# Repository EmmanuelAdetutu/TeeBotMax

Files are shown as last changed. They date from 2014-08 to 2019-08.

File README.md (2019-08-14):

TeeBotMax
=========

The design is highly inspired by the fantastic Foldarap and Prusa I3 3D printers. I needed a 3D printer I can fold and carry around easily.
The idea was to develop a high qiality 3D printer which is simple to build and at the same time, easy to move around and travel with, built with simple materials and equally strong and precise.

Blog, Photo, Info:  http://tutuemma.wordpress.com/3d-stuffs/teebotmax/

Build Video Part 1: https://www.youtube.com/watch?v=Mo2O-83_jfQ

<b>TeeBot suitcase 3D printer.</b><br>
The second iteration of the design resulted in a version that fits and works in a suitcase!! the project was successfully funded via kickstater (https://www.kickstarter.com/projects/99905999/teebot-the-suitcase-3d-printer)

Version2  
=========

Many thanks to builders and contributors who have been giving the feedbacks, there is an update version of the TeebotMax featured with Auto-Bed leveling, strong modified plastic parts and other cool fixes.

<b>***folow me on instagram...  </b>[#teebot3d](https://www.instagram.com/teebot3d/)

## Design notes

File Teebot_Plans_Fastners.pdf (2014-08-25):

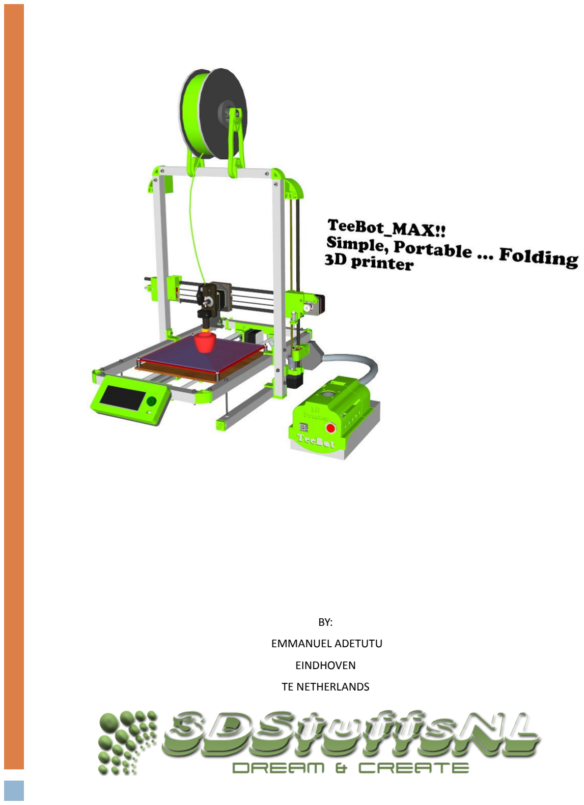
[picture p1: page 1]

BY:

EMMANUEL ADETUTU

EINDHOVEN

TE NETHERLANDS

7/18/2014 | TeeBotMax | 1

### TABLE OF CONTENTS

ABOUT The MANUAL | 2
The design & Specification | 3
Specification | 1
Fastners | 2

ABOUT THE MANUAL.

This manual provides you with a visual step by step guide on how to build or assemble TeeBotMax 3D printer. For more build photos please visit my blog, you will have to source the material/parts needed for your build according to the design.

Many will like to start with a complete/ partial kit, you can grab one directly here (www.3dstuffs.nl/webstore/)

Please report any error detected in this documentation.

I do all of my drawing in Sketchup and a big fan of the software.

Feel free to get in touch, if you have related questions, collaboration enquiry, or just simply talk 3D printing

For photos and videos of the 3D printer in action, visit my web blog

### How to contact

Twitter : @teebotmax

Google plus TeebotMax (https://plus.google.com/u/0/b/106611509110430377536/106611509110430377536/posts)

Web Blog tutuemmaWordpress (https://tutuemma.wordpress.com/)

You can grab a 3D printer kit or needed parts here (www.3dstuffs.nl/webstore/)

I hope this guide helps or inspire you in building or assembling your own 3D printer!! If you do please send me a photo of your build.

THE DESIGN & SPECIFICATION.

The Idea was to design and build a 3D printer which is simple to assemble, easy to move around and travel with, using simple easy to get materials and equally strong and precise.
Many open source designed 3D printer have inspired me in the design of TeeBotMax. Many thanks for sharing: to all the open source developers worldwide over.
**Special thanks to - Josef Prusa (Prusa I3), Emmanuel Gilloz (FoldaRap), Richard Horne (Richrap), Reifsnyderb (J head Hotend) just to mention a few.

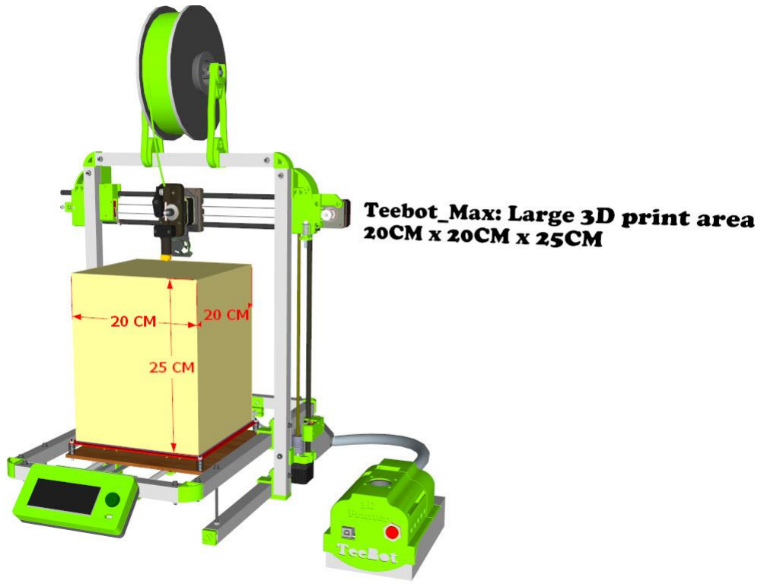
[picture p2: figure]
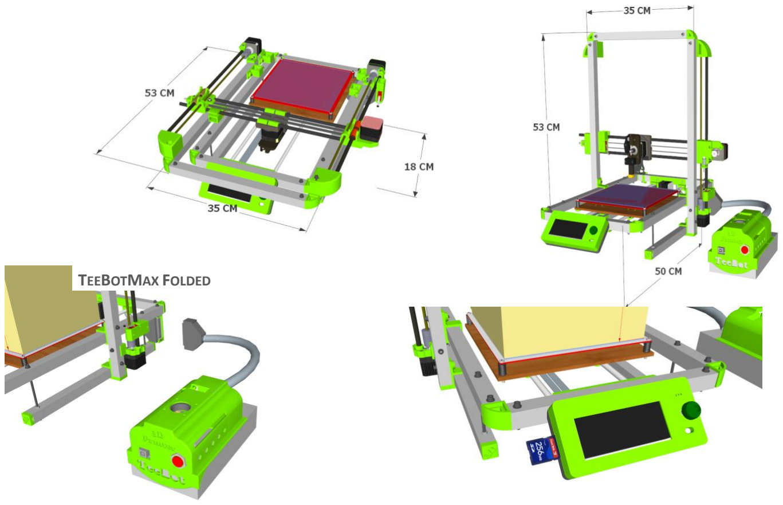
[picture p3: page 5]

TEEBOTMAX FOLDED

SPECIFICATION.

- Build Cost: 350 ~500 Euro (Depending on source of materials/parts)
- Build time: Approximately 1 full day.
- Filament type: Compatible with 3mm/1.75mm, ABS/PLA/Flexible_filament
- Print Speed: 120mm/s
- Nozzle: J head type 0.4mm
- Tested Layer height/resolution: 0.1mm
- Power supply: 12v 20a
- Weight: ~7kg

FASTNERS.

### Footer

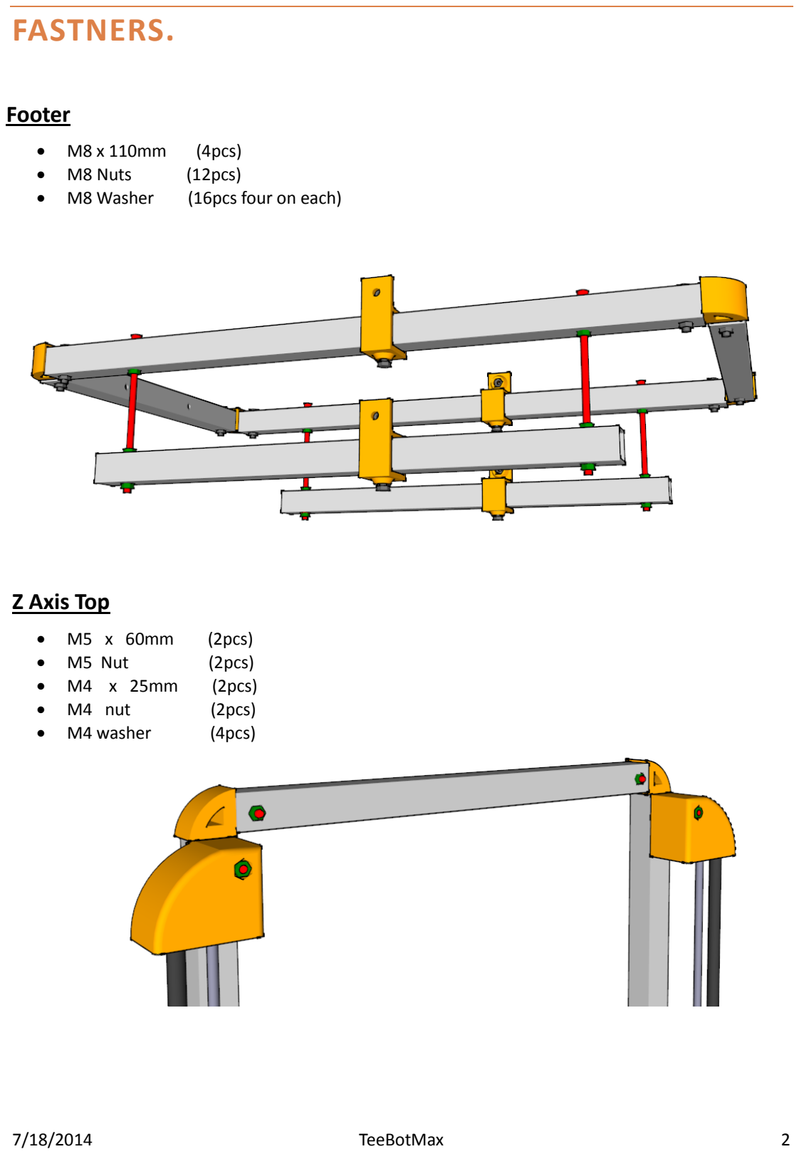
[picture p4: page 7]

- | M8 x 110mm | (4pcs)
- | M8 Nuts | (12pcs)
- | M8 Washer | (16pcs four on each)

### Z Axis Top

- | M5 x 60mm | (2pcs)
- | M5 Nut | (2pcs)
- | M4 x 25mm | (2pcs)
- | M4 nut | (2pcs)
- | M4 washer | (4pcs)

### Z Axis Bottom

- M4 x 30mm (4pcs)
- | M4 washer | (4pcs)
- | M4 Nut | (4pcs)

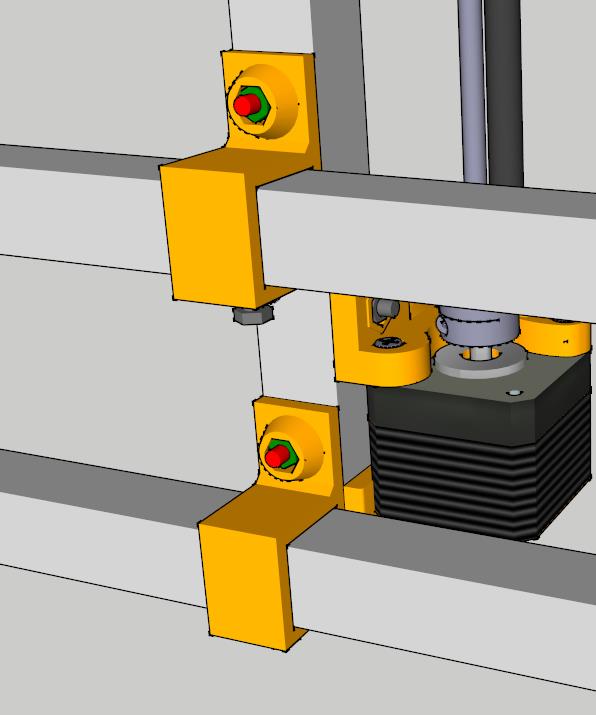
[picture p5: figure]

### Z Axis lock

- M4 x 10mm (4pcs)
- | M4 nuts | (4pcs)

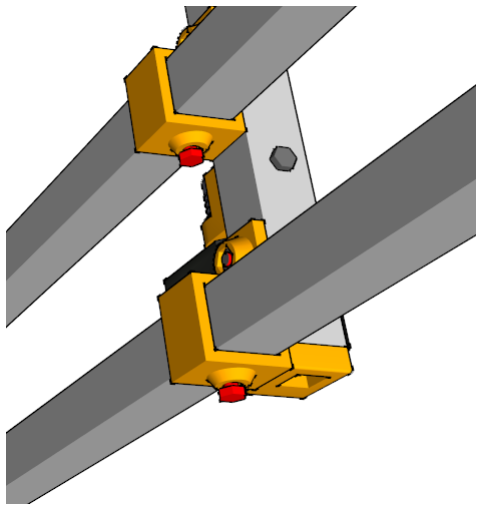
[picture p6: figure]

### Z Motor Holder

- | M4 | x 30mm (2pcs)
- | M4 Nuts | (2pcs)
- | M4 Washer | (2pcs)
- M3 x 10mm (6pcs)

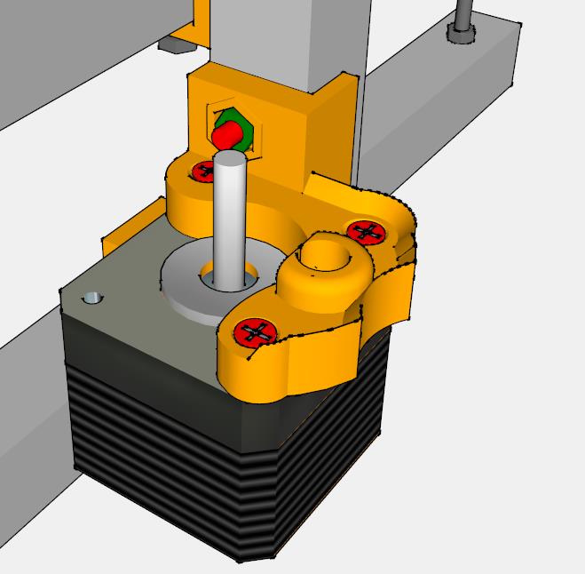
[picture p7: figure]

### Four corner

- | M4 x 25mm | (8pcs)
- | M4 Nuts | (8pcs)
- | M4 washers | (16pcs)

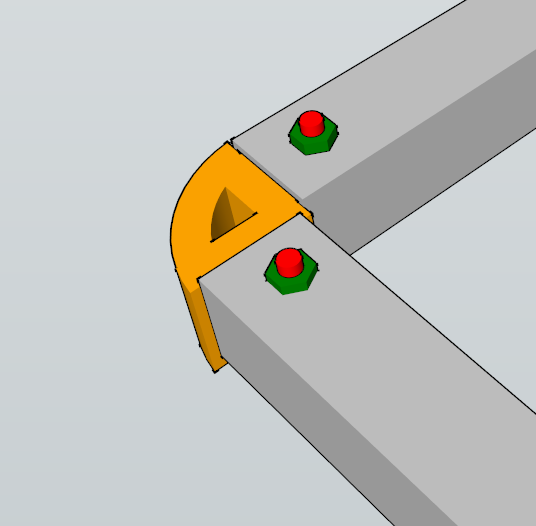
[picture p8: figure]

### X Axis

- | M3 x 10mm | (3pcs)
- Flat head M4 x 25mm (2pcs)
- | M4 Nut | (2pcs)
- | M3 x 20mm | (1pcs)
- | M3 nut | (2pcs)

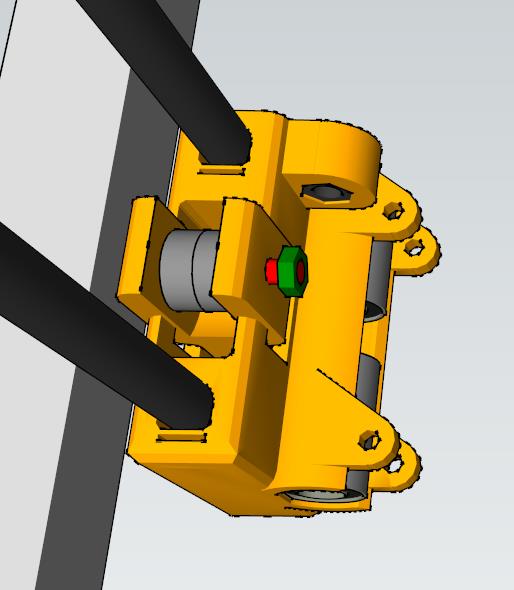
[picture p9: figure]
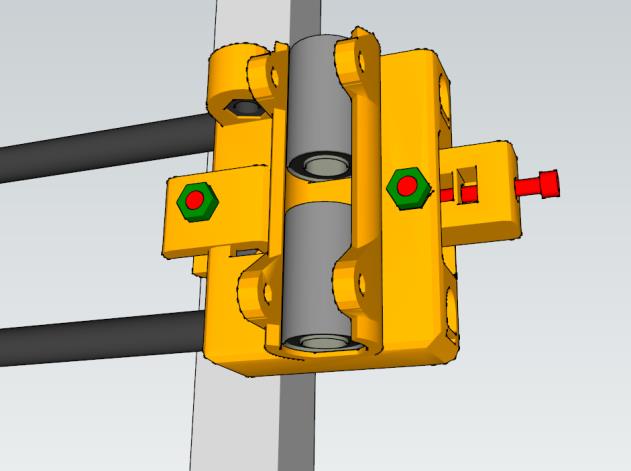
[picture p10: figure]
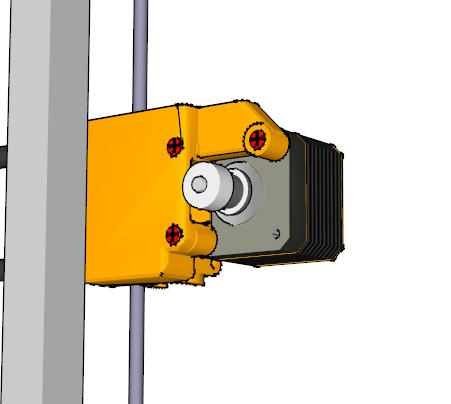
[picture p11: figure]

### Y axis

- M4 x 30mm (1pcs)
- | M4 Nuts | (1pcs)
- | M3 x 30mm | (4pcs)
- | M3 nuts | (4pcs)
- | M3 washer | (8pcs)
- | M3 x 10mm | (3pcs)

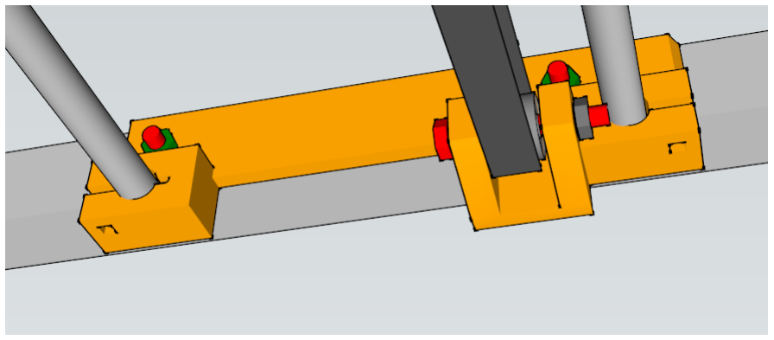
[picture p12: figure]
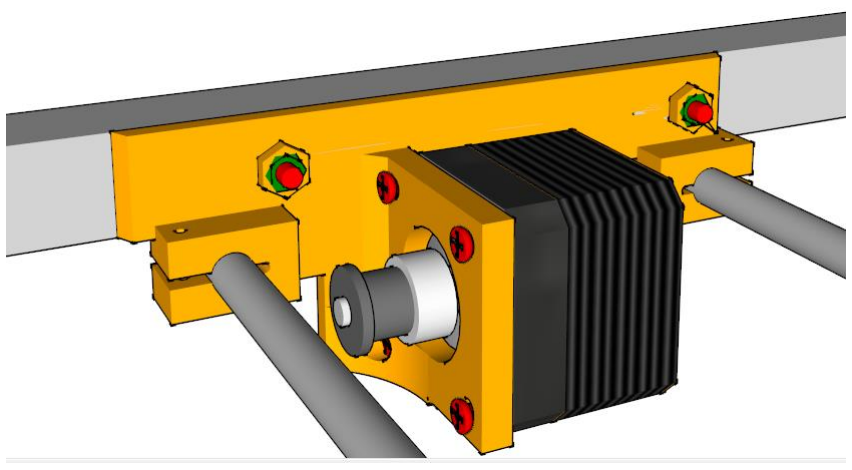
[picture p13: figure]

### Heat Bed

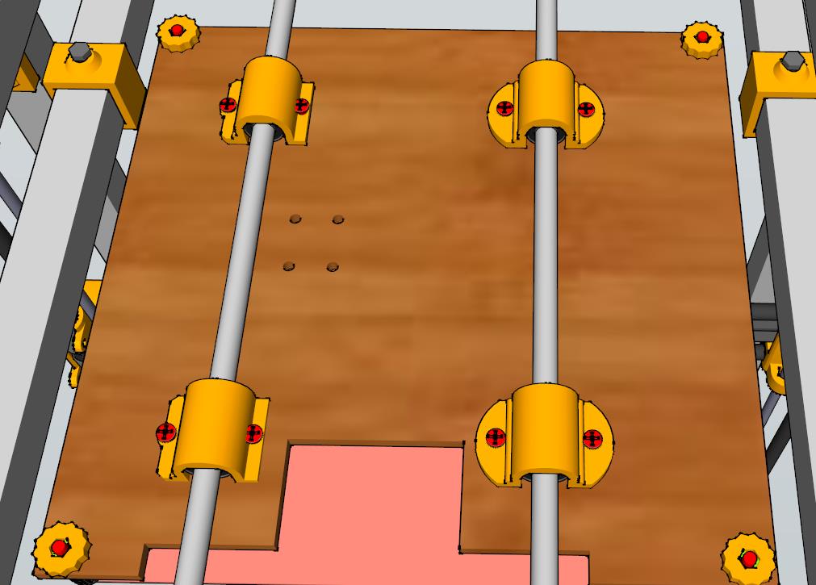
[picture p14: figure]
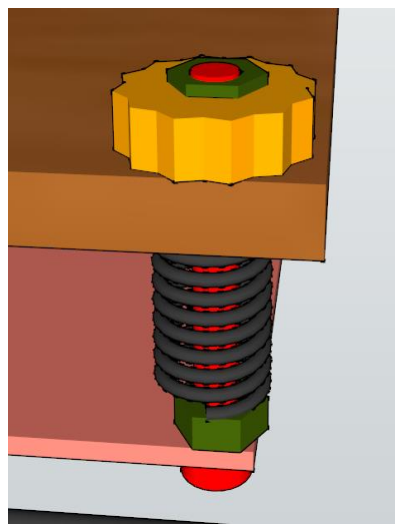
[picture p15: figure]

- M3 x 30mm (4pcs)
- | M3 nuts | (8pcs)
- M3 x 16mm (8pcs)
- M3 washer (8pcs)
- | M3 nuts | (8pcs)

### X Axis carriage

- | M3 x 20mm fan | (2pcs)
- | M3 washer | (4pcs)
- | M3 nut | (2pcs)
- | M4 x 25mm | (4pcs) mount
- | M4 nuts | (4pcs)
- | M 5 nuts | (2pcs) X_axis lift

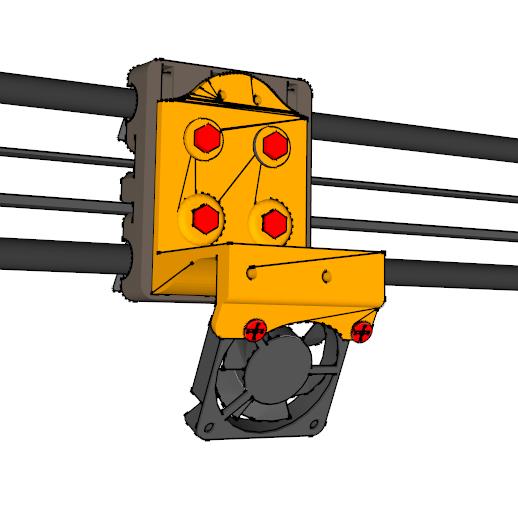
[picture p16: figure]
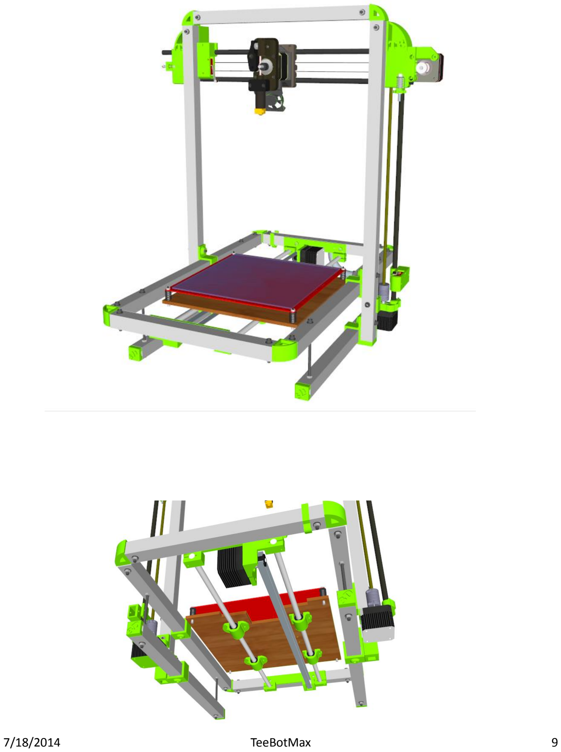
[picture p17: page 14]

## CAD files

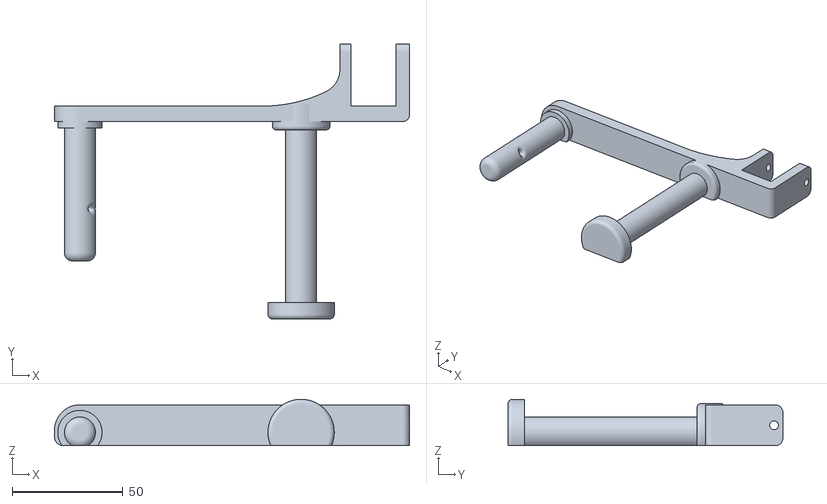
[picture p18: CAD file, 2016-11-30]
STL_Files/SPOOL_FEEDER.stl
160.5 x 124.2 x 21.0

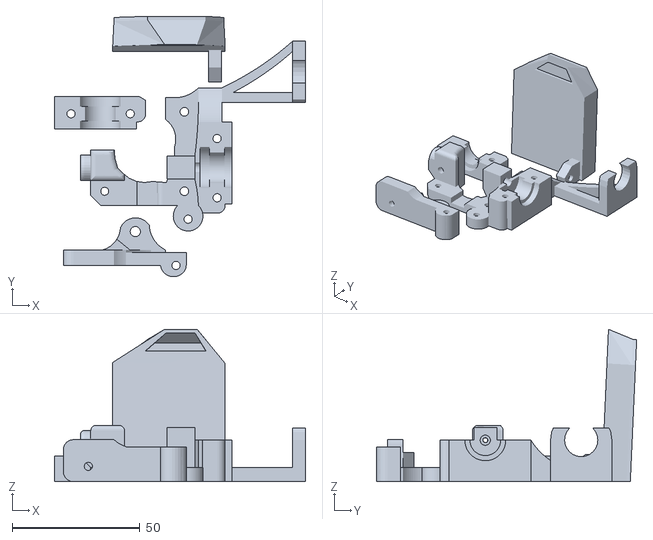
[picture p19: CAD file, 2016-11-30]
STL_Files/Extruder_E3d_Lite.stl
98.2 x 101.8 x 59.6

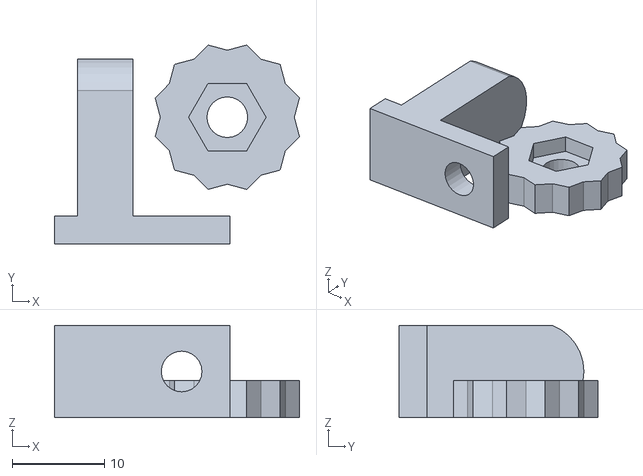
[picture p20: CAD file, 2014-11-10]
STL_Files/Smart_Zlevel.stl
26.5 x 21.5 x 10.0

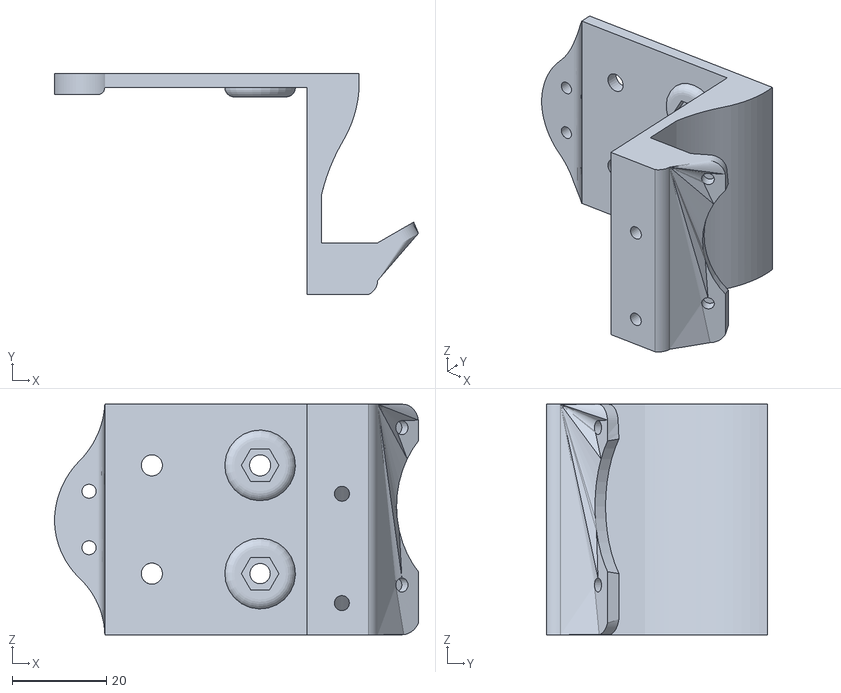
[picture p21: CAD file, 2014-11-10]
STL_Files/X_Extruder_Mount_2.stl
77.4 x 47.0 x 49.0

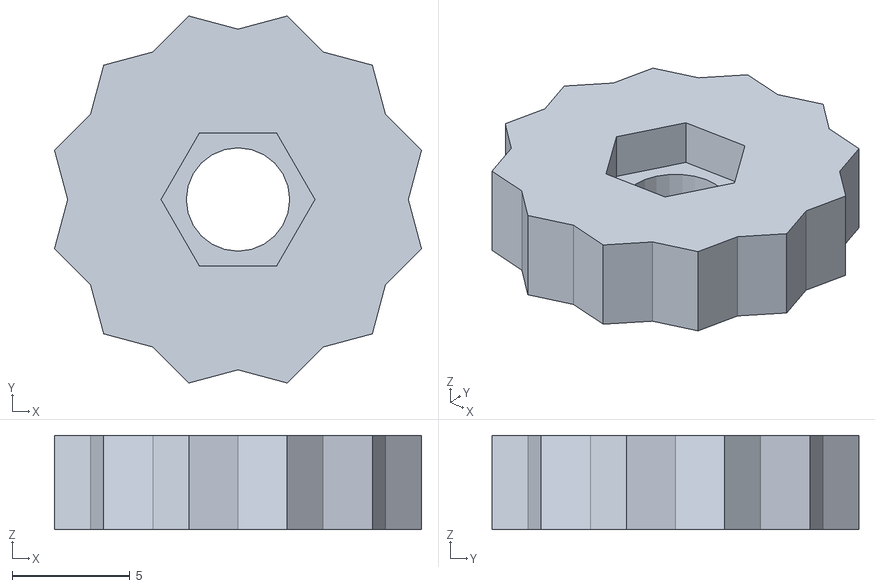
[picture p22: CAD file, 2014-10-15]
STL_Files/Bed_Knobs.stl
15.6 x 15.6 x 4.00

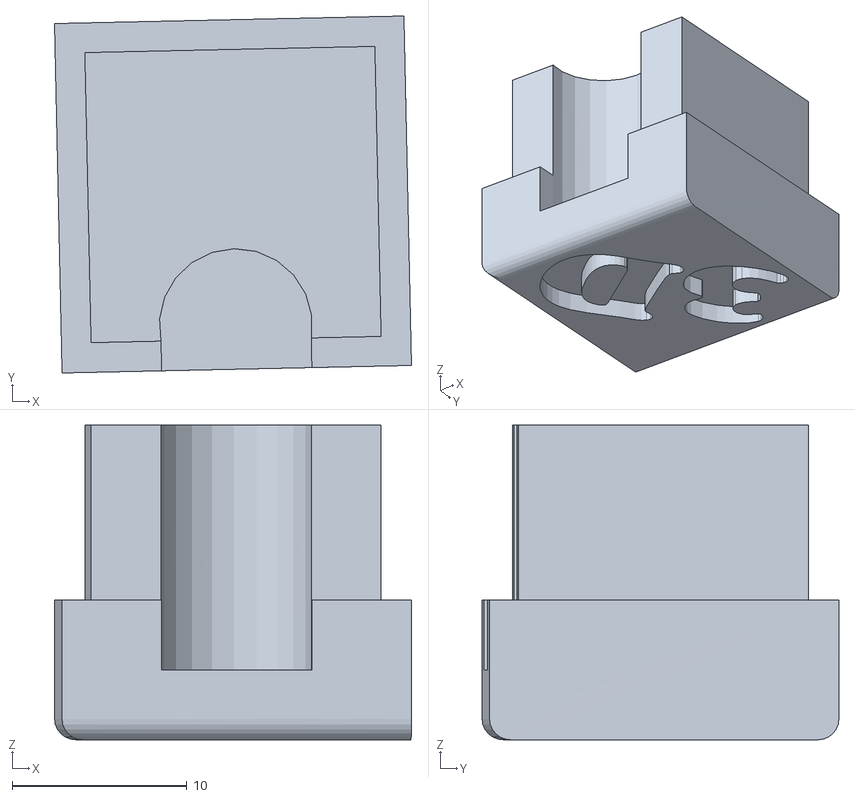
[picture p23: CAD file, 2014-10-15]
STL_Files/Foot_Cap.stl
20.4 x 20.4 x 18.0

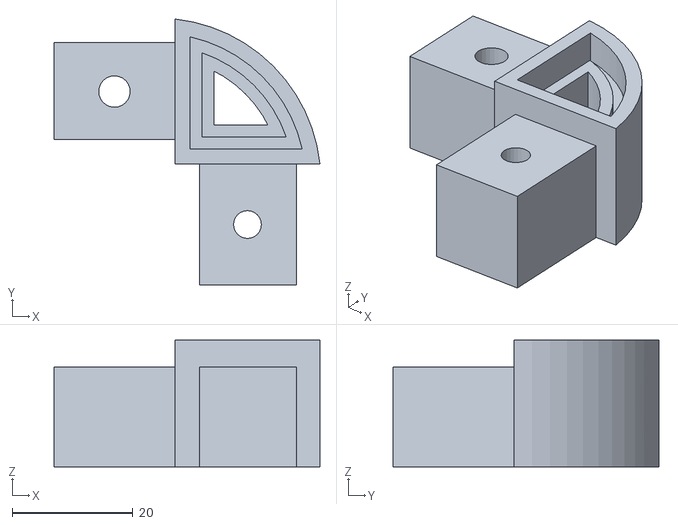
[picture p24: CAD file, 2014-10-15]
STL_Files/Corners.stl
44.0 x 44.0 x 21.0

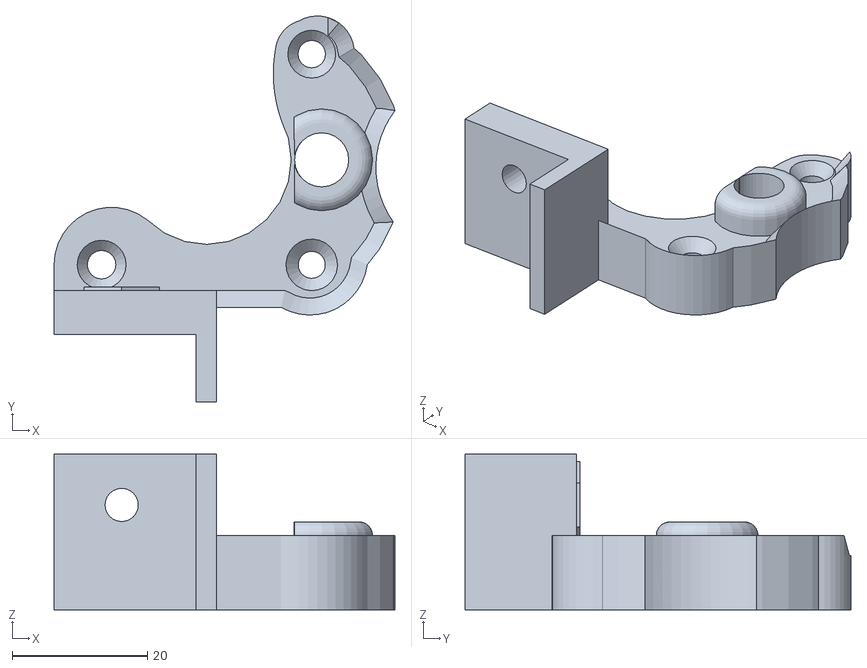
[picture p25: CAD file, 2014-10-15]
STL_Files/Z_End_Motor_R.stl
50.4 x 57.1 x 23.0

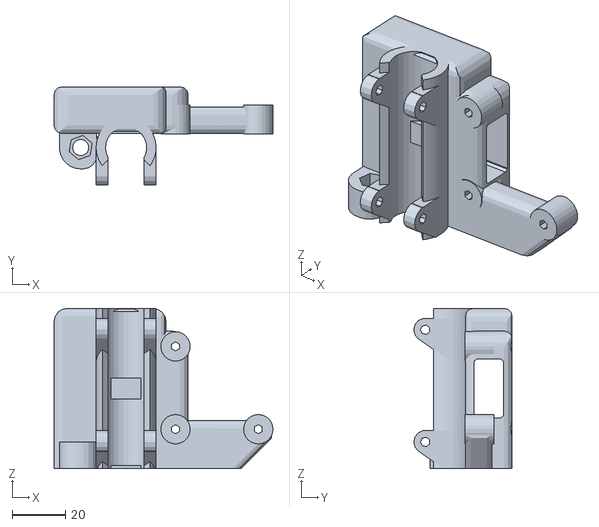
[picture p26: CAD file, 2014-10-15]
STL_Files/X_Ends_R.stl
82.0 x 36.9 x 60.0

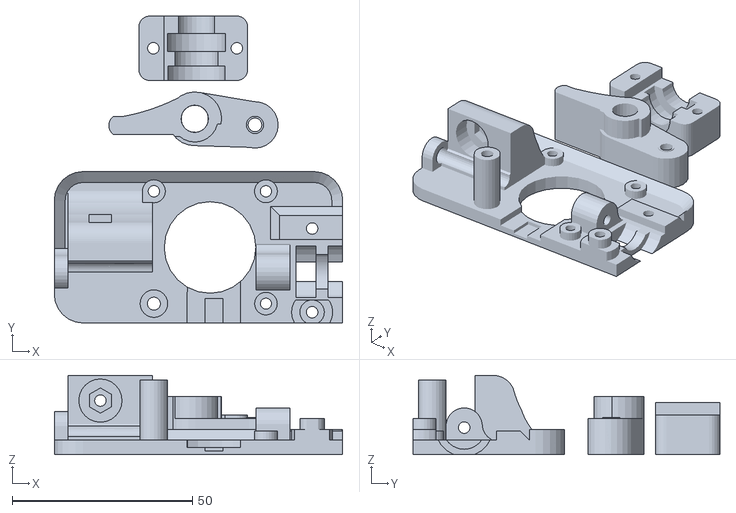
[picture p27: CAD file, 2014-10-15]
STL_Files/Direct_Drive_Extruder.stl
80.0 x 85.1 x 22.0

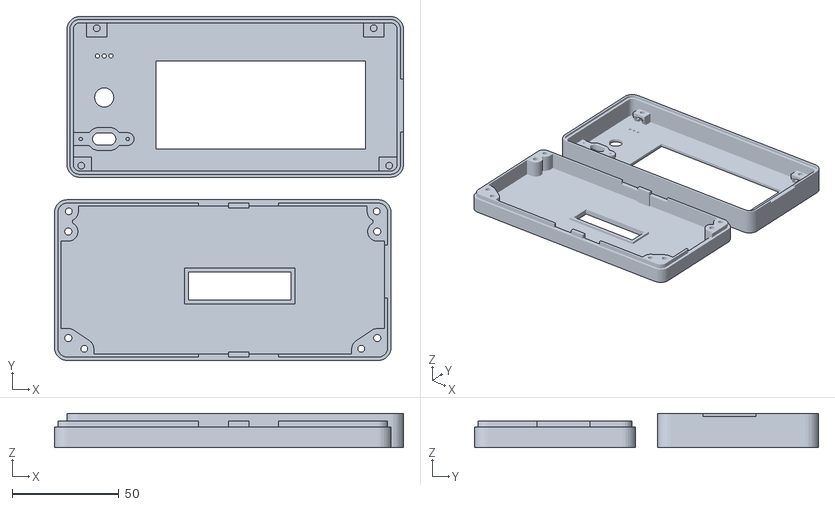
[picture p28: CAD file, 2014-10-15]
STL_Files/SD_Ramps_Case.stl
163.8 x 161.5 x 16.0

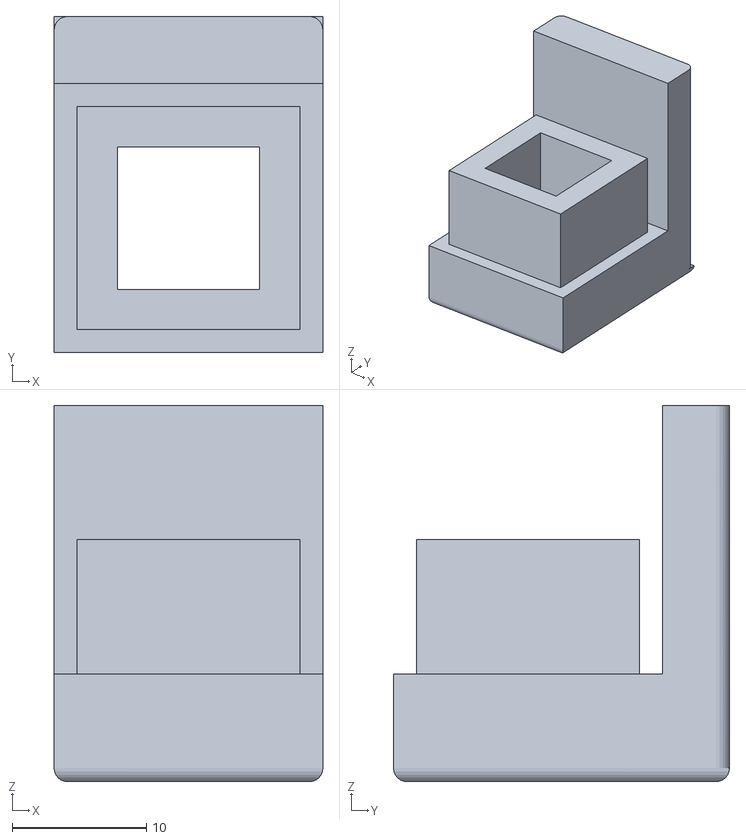
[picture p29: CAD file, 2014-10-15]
STL_Files/Z_Foot_Cap.stl
20.0 x 25.0 x 28.0

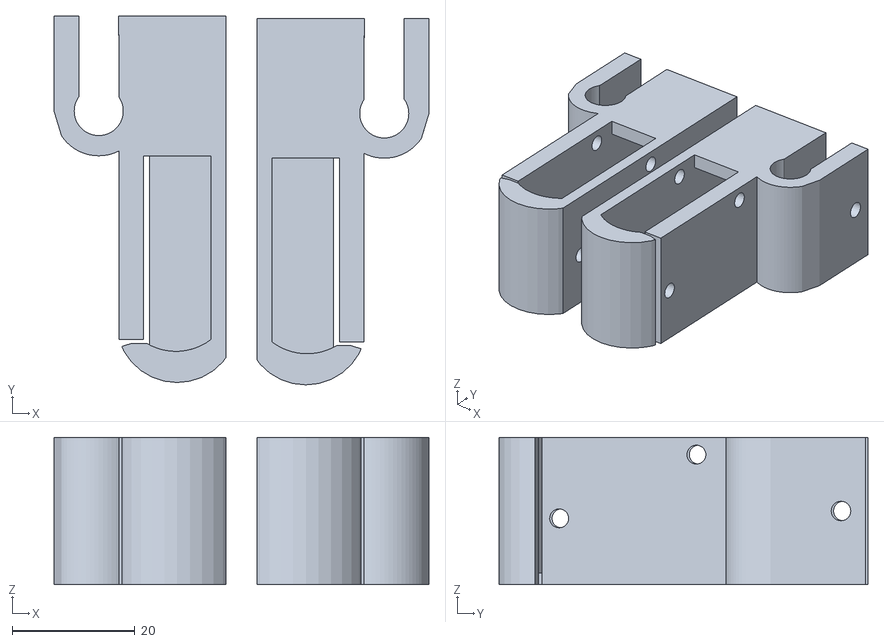
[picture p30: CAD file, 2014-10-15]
STL_Files/Limit Holder.stl
61.2 x 60.2 x 24.0

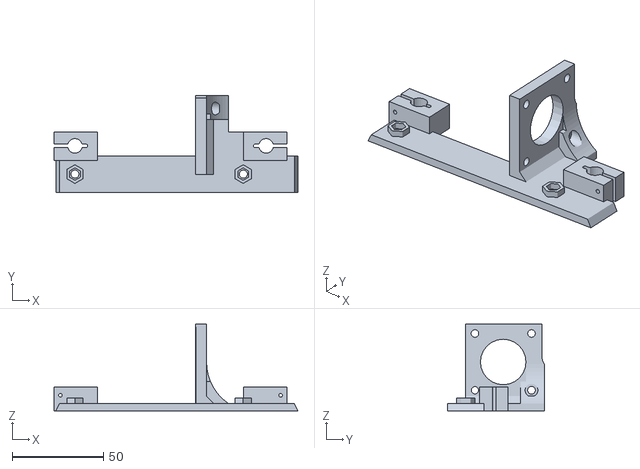
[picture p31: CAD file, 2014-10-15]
STL_Files/Y_End_Motor.stl
134.0 x 53.1 x 47.5

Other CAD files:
STL_Files/Z_End_Motor_L.stl
STL_Files/X_Motor_Iddler.stl
STL_Files/Connectors.stl
STL_Files/Optional Spool holder.stl
STL_Files/Bearing_Holder.stl
STL_Files/Belt_Bearing_Holder.stl
STL_Files/Extruder Extension.stl
STL_Files/Optional_Dsub_Holder.stl
STL_Files/Ramps_casing.stl
STL_Files/X_Ends_L.stl
STL_Files/X_Extruder_Mount.stl
STL_Files/X_carriage.stl
STL_Files/Y_Iddler.stl
STL_Files/Z_Rod_Holder_L.stl
STL_Files/Z_Rod_Holder_R.stl

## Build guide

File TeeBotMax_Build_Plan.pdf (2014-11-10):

BY:

EMMANUEL ADETUTU

EINDHOVEN

TE NETHERLANDS

7/18/2014 | TeeBotMax | 1

### TABLE OF CONTENTS

ABOUT The MANUAL | 2
The design & Specification | 3
Specification | 2
List of Materials Needed | 3
Fastners | 4
Printed parts | 11
Smooth & Threaded ROds | 13
Aluminium frame | 13
print bed support | 0
print bed support | 1
The Build… Part 1 (Main frame) | 4
The Build… Part 2 (Print platform) | 10
The Build… Part 3 (Assembling the X Axis) | 15
The Build… Part 4 (Assembling the Z Axis) | 20
The Build Part 5 (Extruder carriage & belt) | 27
The Build Part 6 (ELECTRONICS & Limit switch) | 32
Limit Switch | 33

ABOUT THE MANUAL.

This manual provides you with a visual step by step guide on how to build or assemble TeeBotMax 3D printer. For more build photos please visit my blog, you will have to source the material/parts needed for your build according to the design.

Many will like to start with a complete/ partial kit, you can grab one directly here (www.3dstuffs.nl/webstore/)

Please report any error detected in this documentation.

I do all of my drawing in Sketchup and a big fan of the software.

Feel free to get in touch, if you have related questions, collaboration enquiry, or just simply talk 3D printing

For photos and videos of the 3D printer in action, visit my web blog

### How to contact

Twitter : @teebotmax

Google plus TeebotMax (https://plus.google.com/u/0/b/106611509110430377536/106611509110430377536/posts)

Web Blog tutuemmaWordpress (https://tutuemma.wordpress.com/)

You can grab a 3D printer kit or needed parts here (www.3dstuffs.nl/webstore/)

I hope this guide helps or inspire you in building or assembling your own 3D printer!! If you do please send me a photo of your build.

THE DESIGN & SPECIFICATION.

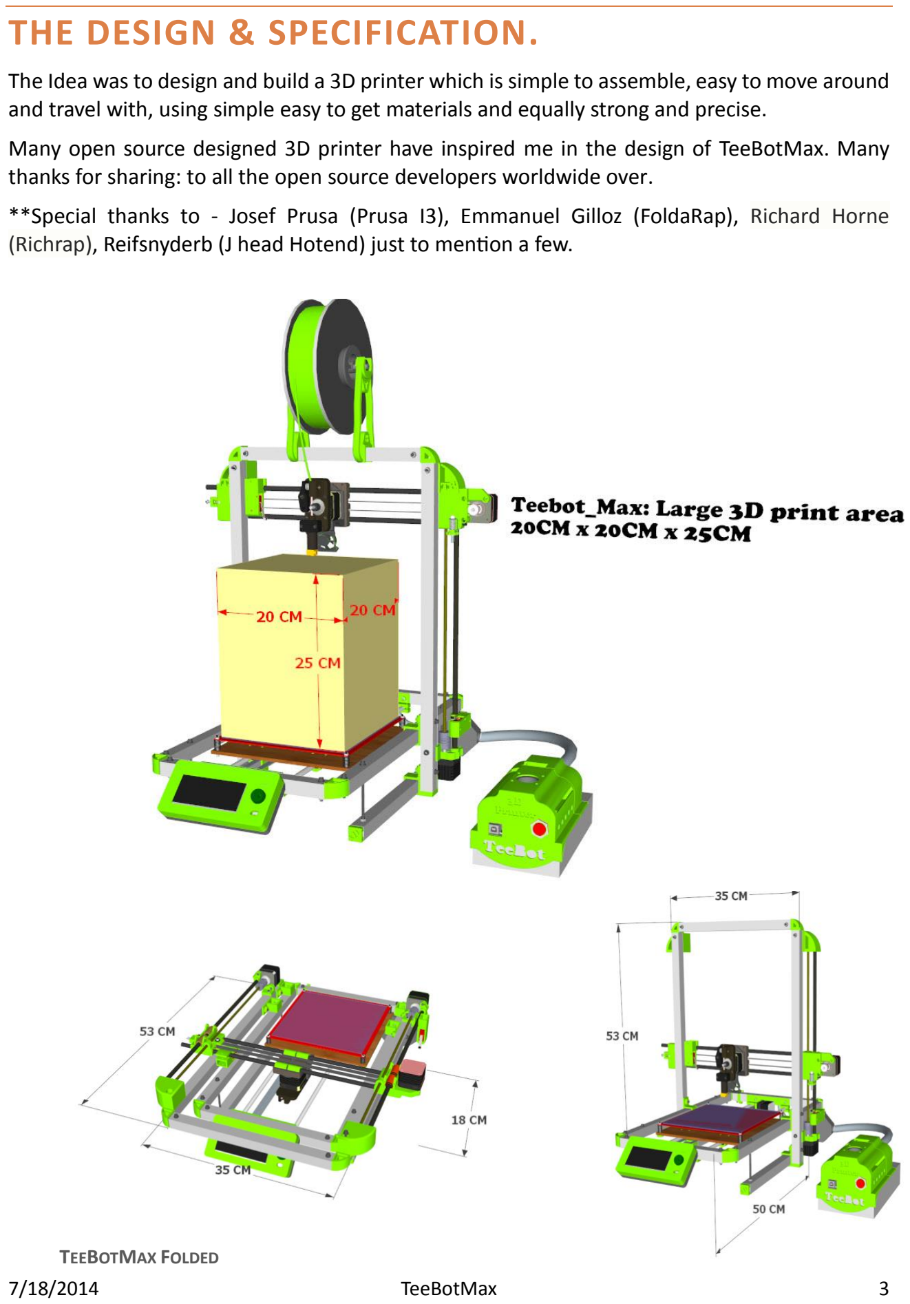
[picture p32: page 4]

The Idea was to design and build a 3D printer which is simple to assemble, easy to move around and travel with, using simple easy to get materials and equally strong and precise.
Many open source designed 3D printer have inspired me in the design of TeeBotMax. Many thanks for sharing: to all the open source developers worldwide over.
**Special thanks to - Josef Prusa (Prusa I3), Emmanuel Gilloz (FoldaRap), Richard Horne (Richrap), Reifsnyderb (J head Hotend) just to mention a few.

TEEBOTMAX FOLDED

SPECIFICATION.

- Build Cost: 350 ~500 Euro (Depending on source of materials/parts)
- Build time: Approximately 1 full day.
- Filament type: Compatible with 3mm/1.75mm, ABS/PLA/Flexible_filament
- Print Speed: 120mm/s
- Nozzle: J head type 0.4mm
- Tested Layer height/resolution: 0.1mm
- Power supply: 12v 20a
- Weight: ~7kg

LIST OF MATERIALS NEEDED.

SN | Material | Description | Quantity | Note/Source
1 | All Printed plastic parts | You can print or Buy | 1 set
2 | Extruder kit (TeeStruder) | Direct drive extruder. | 1 set
3 | Printer Frame aluminum | 20mm square | 3.4 meters
4 | 8mm Smooth rods | Used in all Axis | 3 meters
5 | Linear bearing Lm8uu | 8 mm | 11 Pcs
6 | Springs Heatbed exturder. | O.D: 10mm | 6 Pcs
7 | 624 Bearing | Used as idlers | 5 Pcs
8 | Threaded rods | 5mm diameter | 1 meter
9 | Flexible shaft coupler | 5mm X 5mm | 5 Pcs
10 | Heated Bed | 12v Heated bed | 1 Pcs
| Print Glass/ mirror | 20cm x 20cm | 1pcs
11 | Complete Electronics Board | Ramps 1.4 | 1 Set
12 | Cooling Fan | 4Cm X 4Cm X 1Cm | 2 Pcs
13 | Power Supply | 12v with min of 15A | 1 Set
14 | Hotend | J head type | 1 Set
15 | 100k Thermistor. | Heated_bed & extruder. | 2 Pcs
16 | Limit switch | One for each axis | 3
17 | Ramps LCD controller | Print without a PC/Laptop | 1
18 | GT2 Timing Belt | Drive’s the X & Y axis | 2 meters
19 | Pulley | Gt2 Pulley | 2
20 | Stepper Motors | Nema 17 | 5 Pcs
| Binder Clips | standard | 4 Pcs

For a complete detail list of fasters please see the section below

FASTNERS.

### Footer

- | M8 x 110mm | (4pcs)
- | M8 Nuts | (12pcs)
- | M8 Washer | (16pcs four on each)

### Z Axis Top

- | M5 x 60mm | (2pcs)
- | M5 Nut | (2pcs)
- | M4 x 25mm | (2pcs)
- | M4 nut | (2pcs)
- | M4 washer | (4pcs)

### Z Axis Bottom

- M4 x 30mm (4pcs)
- | M4 washer | (4pcs)
- | M4 Nut | (4pcs)

### Z Axis lock

- M4 x 10mm (4pcs)
- | M4 nuts | (4pcs)

### Z Motor Holder

- | M4 | x 30mm (2pcs)
- | M4 Nuts | (2pcs)
- | M4 Washer | (2pcs)
- M3 x 10mm (6pcs)

### Four corner

- | M4 x 25mm | (8pcs)
- | M4 Nuts | (8pcs)
- | M4 washers | (16pcs)

### X Axis

- | M3 x 10mm | (3pcs)
- Flat head M4 x 25mm (2pcs)
- | M4 Nut | (2pcs)
- | M3 x 20mm | (1pcs)
- | M3 nut | (2pcs)

### Y axis

- M4 x 30mm (1pcs)
- | M4 Nuts | (1pcs)
- | M3 x 30mm | (4pcs)
- | M3 nuts | (4pcs)
- | M3 washer | (8pcs)
- | M3 x 10mm | (3pcs)

### Heat Bed

- M3 x 30mm (4pcs)
- | M3 nuts | (8pcs)
- M3 x 16mm (8pcs)
- M3 washer (8pcs)
- | M3 nuts | (8pcs)

### X Axis carriage

- | M3 x 20mm fan | (2pcs)
- | M3 washer | (4pcs)
- | M3 nut | (2pcs)
- | M4 x 25mm | (4pcs) mount
- | M4 nuts | (4pcs)
- | M 5 nuts | (2pcs) X_axis lift

PRINTED PARTS.

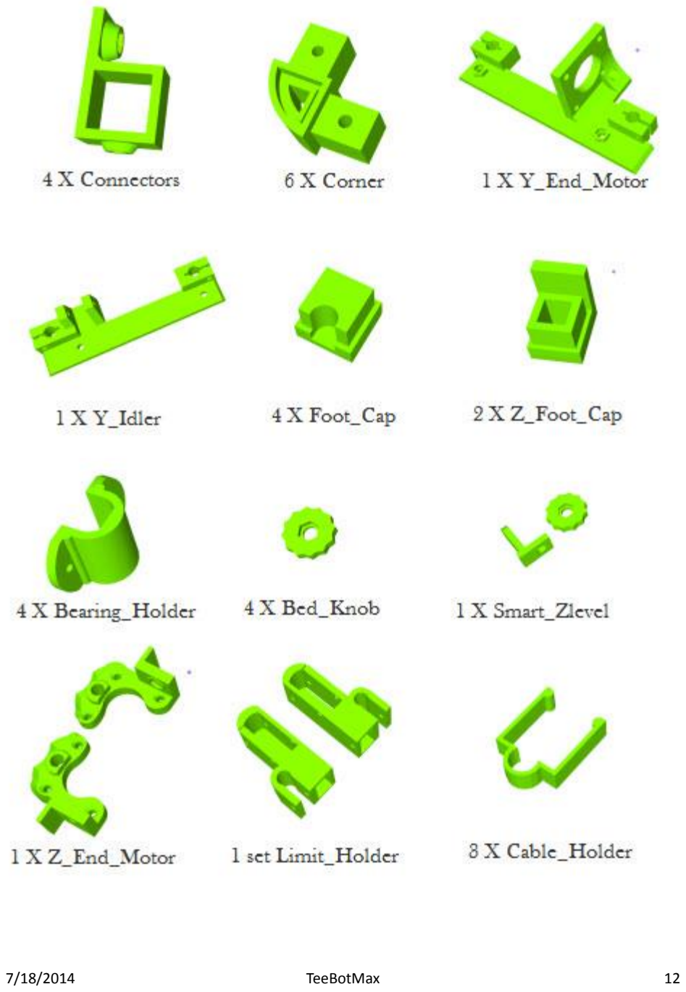
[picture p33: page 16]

SMOOTH & THREADED RODS.

- 2x Smooth rod Ø8 x 460mm
- 4x Smooth rod Ø8 x 420mm
- 2x Threaded rod M5 x 400mm

ALUMINIUM FRAME.

The frame pipes are cut out of 2cm square tubing. 9 Pcs

A. 25cm x 2Pcs | {short main frame}
B. 46cm x 2Pcs | {Long main frame}
C. 50cm x 2Pcs | {Long folding arms}
D. 30cm x 1Pcs | {Folding arms connect}
E. 36cm x 2Pcs | {Foot pipes}

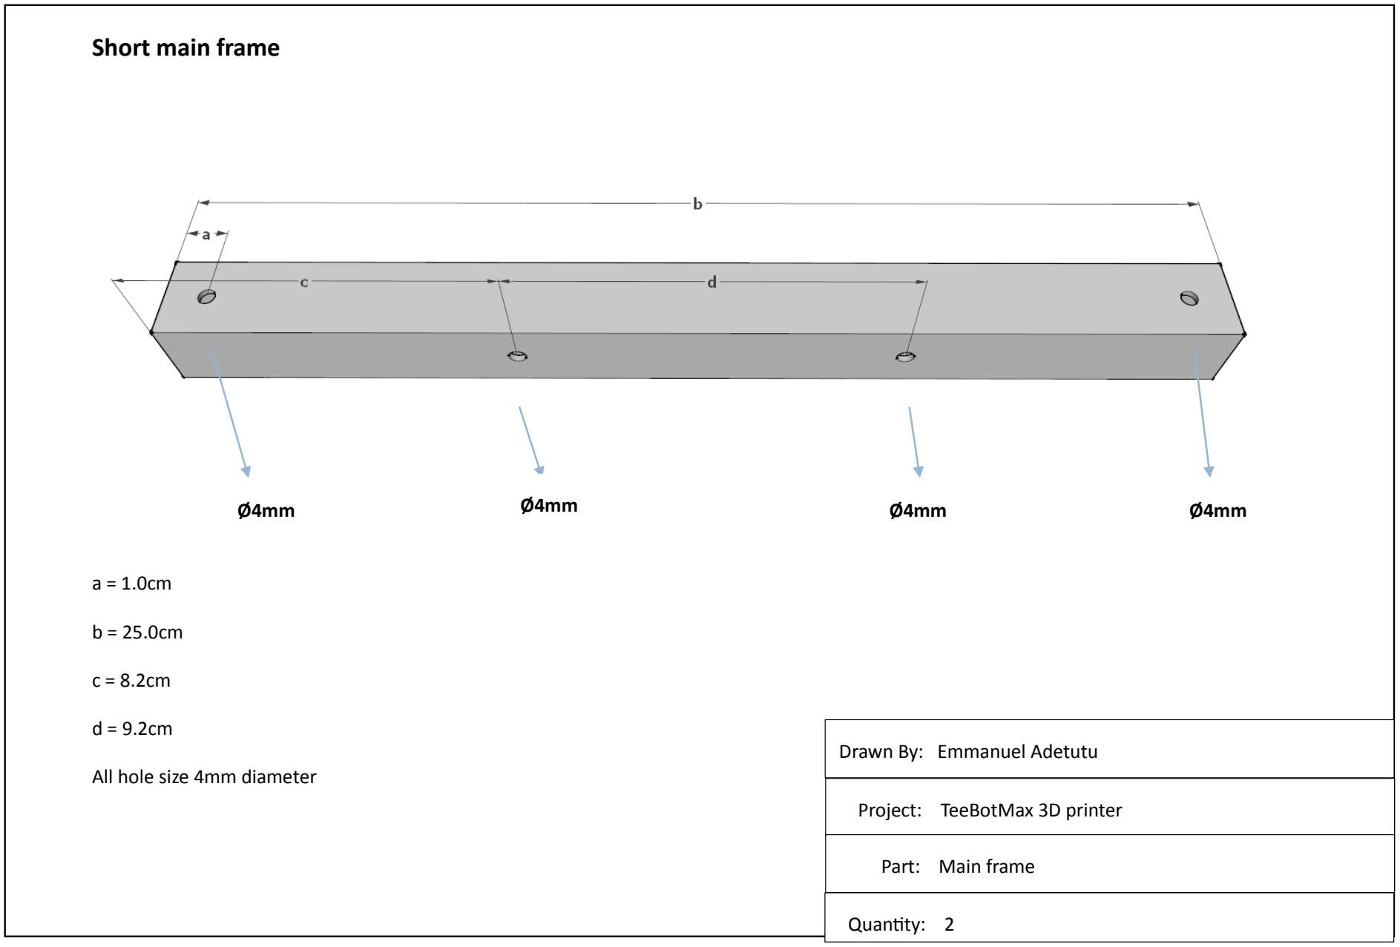
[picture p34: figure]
Short main frame; All hole size 4mm diameter; Drawn By: Emmanuel Adetutu; Project: TeeBotMax 3D printer; Part: Main frame; Quantity: 2

### Long main frame

a = 1.0 cm

b = 6.0 cm

c = 6.0cm

d = 46.0cm

Project: TeeBotMax 3D printer

Part: Main frame

Quantity: 2

Ø8mm | Ø4mm
Ø4mm | Ø8mm

### Long folding arms

a = 1.0cm

b = 6.2cm

c = 50.0cm

d = 3.0cm

e = 11.0cm

Quantity: 2

Part: Z axis frame

Project: TeeBotMax 3D printer

Drawn By: Emmanuel Adetutu

Ø4mm

Ø4mm

Ø4mm

### Short folding arms

a = 1.0cm

b = 30.0cm

c = 1.0cm

Quantity: 1

Part: Z axis frame top

Project: TeeBotMax 3D printer

Drawn By: Emmanuel Adetutu

Ø4mm
Ø4mm

a = 2.0cm

b = 2.0cm

c = 36.0cm

The hole size 8mm diameter

Quantity: 2

Part: footer

Project: TeeBotMax 3D printer

Drawn By: Emmanuel Adetutu

Ø8mm | Ø8mm

PRINT BED SUPPORT

PRINT BED SUPPORT

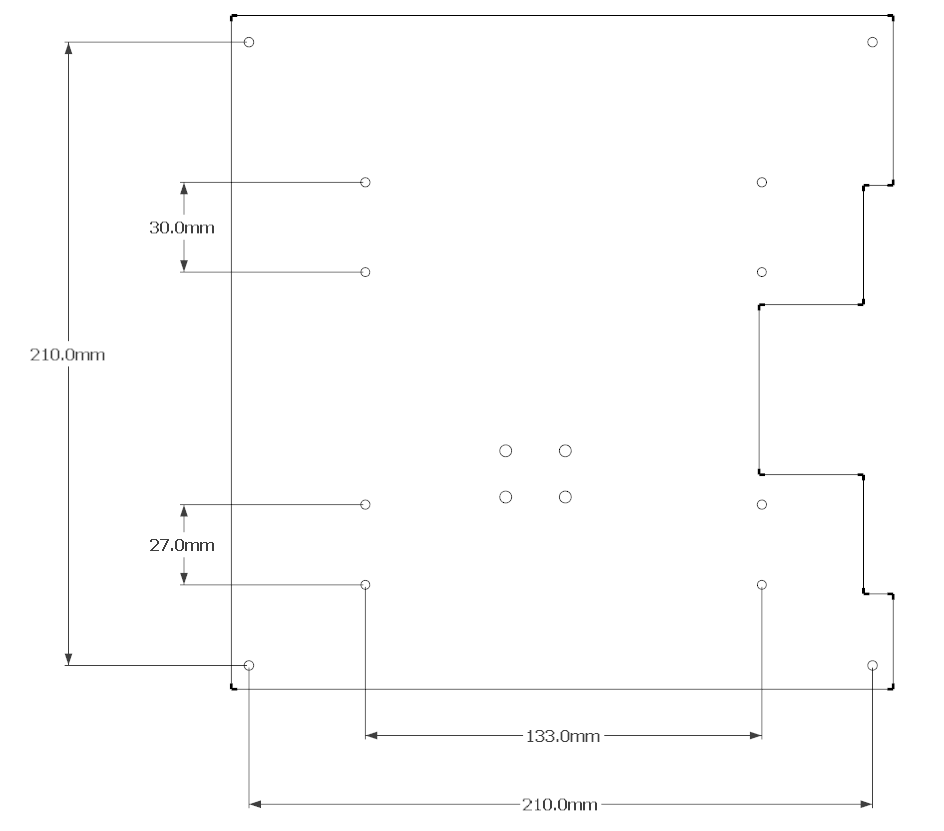
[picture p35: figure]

7/18/2014 | TeeBotMax

2

A = 215mm B = 178mm C = 112mm D = 92mm E = 45mm F = 6mm

A = 35mm

B = 62mm

C = 86mm

D = 56mm

E = 146 mm

F = 162mm

# THE BUILD… PART 1 (MAIN FRAME)

1. Insert 2pcs of the 4m nuts in one of the connectors as shown below, repeat for all 4 connector.
2. Insert 2 of the connectors into the 46cm and 36cm pipe.

## 4 X

3. Thread the M8 bolt into the pipes using 3 nuts and 4 washers. Ensure that the distance between the pipes is 6cm.

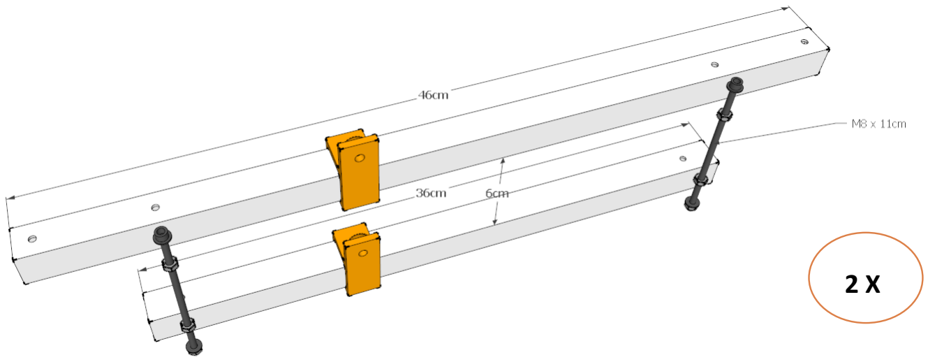
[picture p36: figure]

4. Using M4 x 10mm bolts lock the plastics in place 25cm from the tip of the longer pipe and 20cm from the smaller one as shown below.

Emmanuel Adetutu is a data analyst who works everyday with GIS data in the Netherlands. Likes creating, developing and exploring new tools and application.

My interest in CNC/3D printing started in 2011, when I built my first CNC machine for some wood working projects I have around the house. I started building 3D printers after reading blogs and post by REPRAP developers on the REPRAP.org wiki.

5. Assemble the Y Axis idler as shown below, using the 624 bearing, one M4 bolt and 2 M3 bolts.

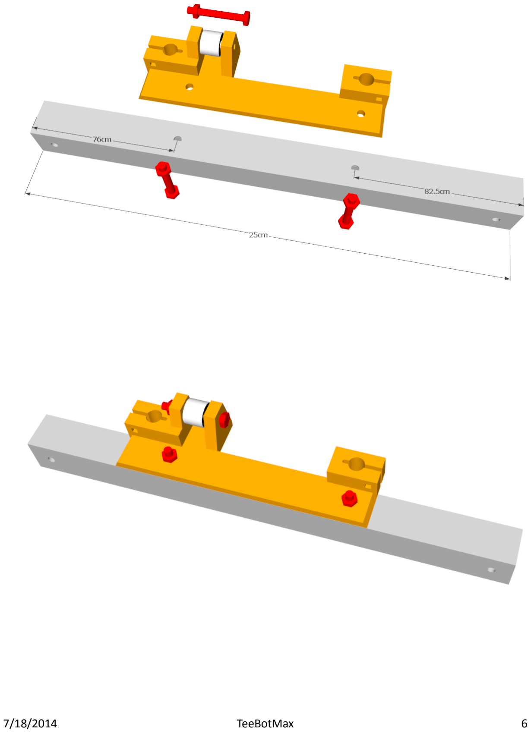
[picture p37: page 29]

6. Assemble the Y Axis Motor end as shown below, using the stepper motor, M3 x 30mm and pulley

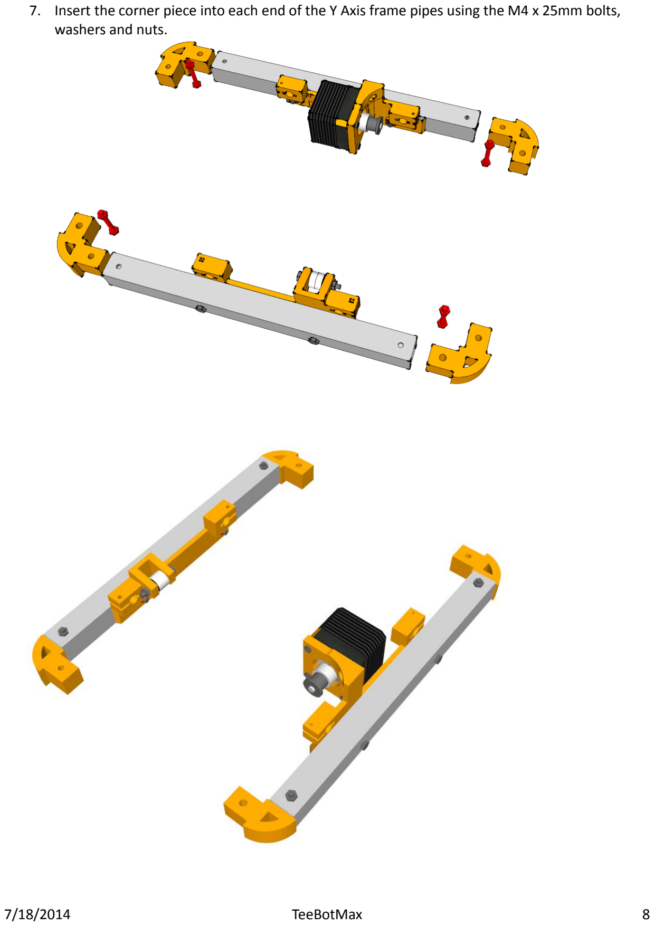
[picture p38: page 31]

7. Insert the corner piece into each end of the Y Axis frame pipes using the M4 x 25mm bolts, washers and nuts.

8. Connect all four parts together using 4 M4 x 25 bolts, washers and nuts

Congrats if you made it this far. !! This completes the build of the main frame make sure all corner joints are tightly fitted and squared. The feet might wobble/shake a bit it is fine, when the Z axis frame is installed it will fix this.

# THE BUILD… PART 2 (PRINT PLATFORM)

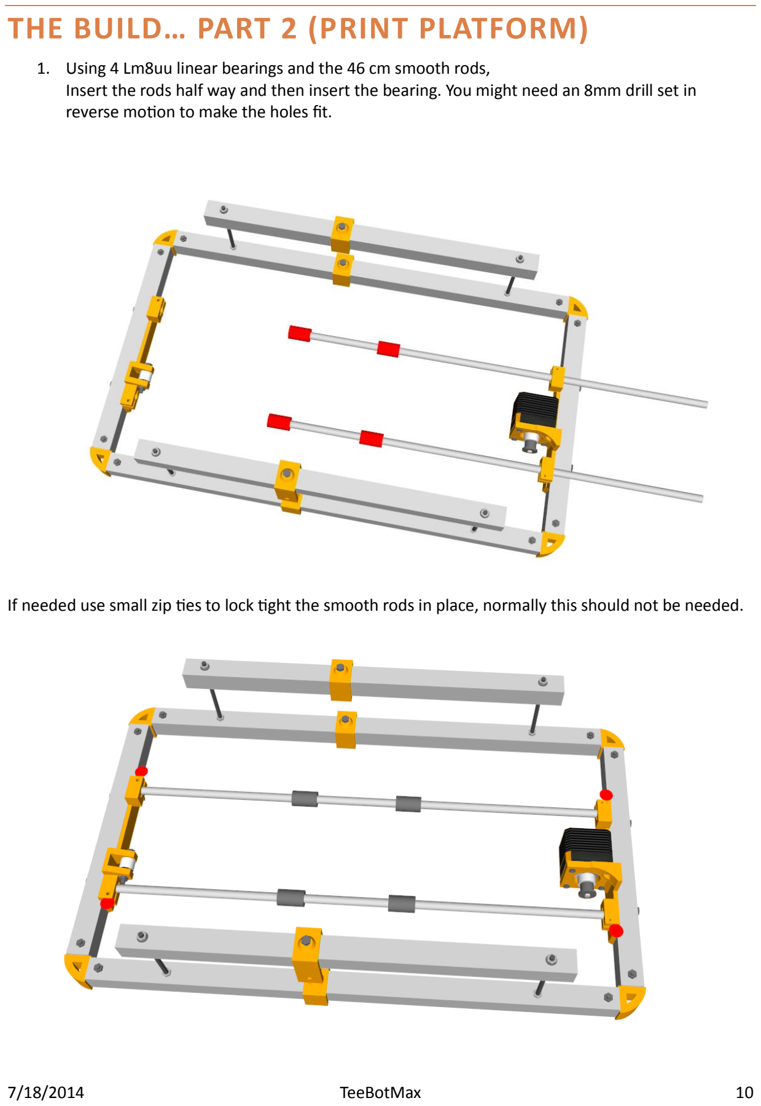
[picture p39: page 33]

1. Using 4 Lm8uu linear bearings and the 46 cm smooth rods,
Insert the rods half way and then insert the bearing. You might need an 8mm drill set in reverse motion to make the holes fit.

If needed use small zip ties to lock tight the smooth rods in place, normally this should not be needed.

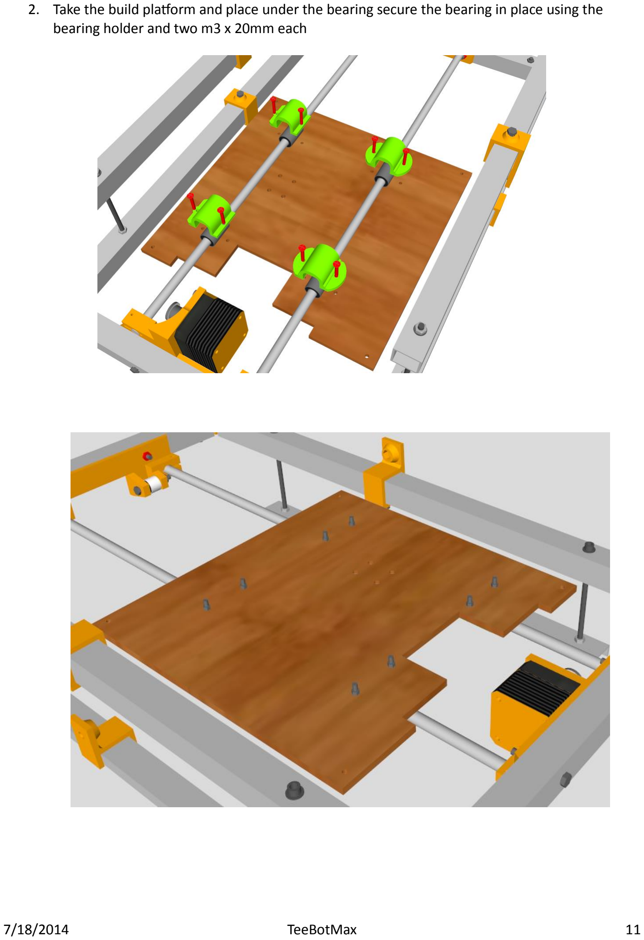
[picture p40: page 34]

2. Take the build platform and place under the bearing secure the bearing in place using the bearing holder and two m3 x 20mm each

3. Belt installation. Install the belt by folding one end of the belt and using a zip tie to hold it in place across the print platform.

Next bring the second end close to the installed end (about2cm spacing) using another zip tie make a notch and tie it, this time not across the build platform, only the belt

Next use a third zip tie to connect the two belt together.

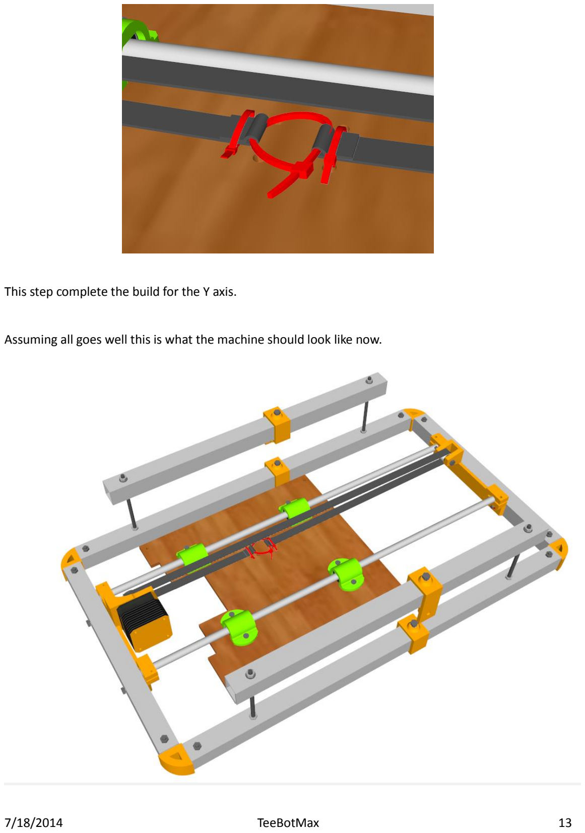
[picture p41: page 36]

This step complete the build for the Y axis.

Assuming all goes well this is what the machine should look like now.

# THE BUILD… PART 3 (ASSEMBLING THE X AXIS)

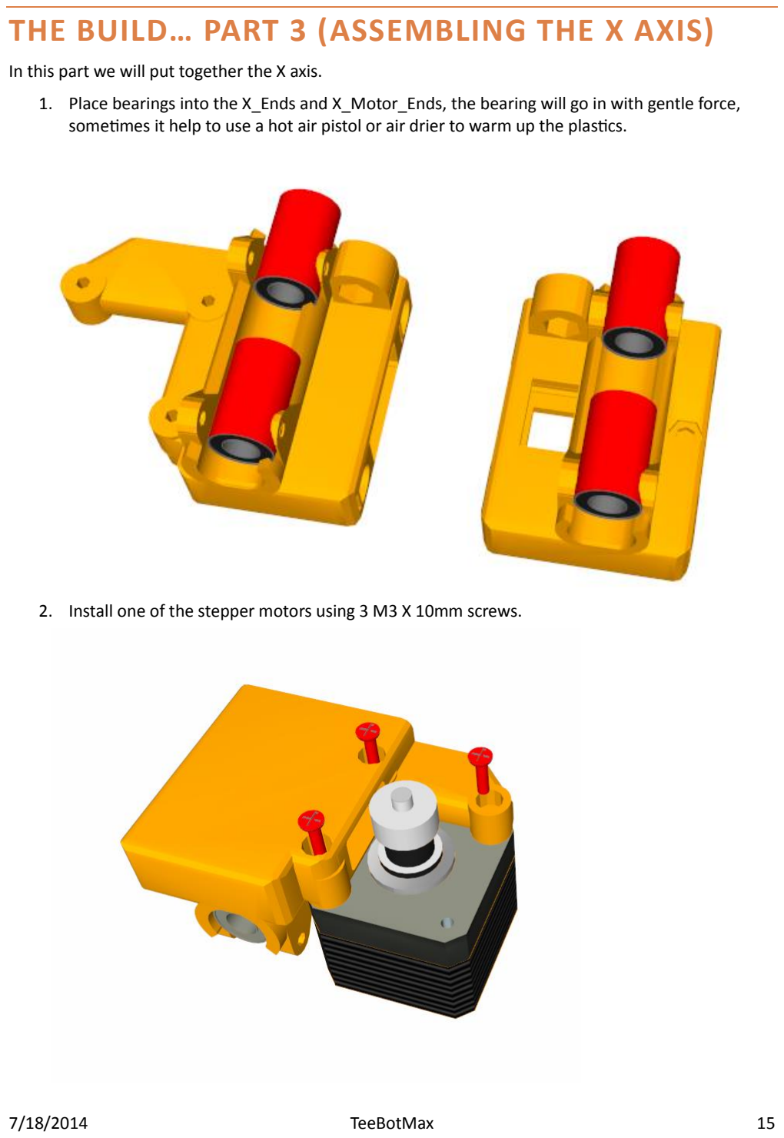
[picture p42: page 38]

In this part we will put together the X axis.

1. Place bearings into the X_Ends and X_Motor_Ends, the bearing will go in with gentle force, sometimes it help to use a hot air pistol or air drier to warm up the plastics.
2. Install one of the stepper motors using 3 M3 X 10mm screws.

3. On the E_End idler thread in one of the M3 x 25mm screw about half way.
4. Insert 2 bearings with an M4 X 25mm screw and lock it in place with a washer & nut.

5. Put the assembly into the X_END

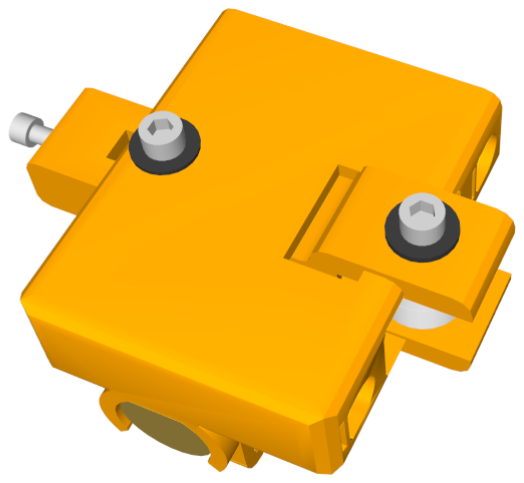
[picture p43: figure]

6. Insert the two X smooth rods into the X axis motor end all the way down.

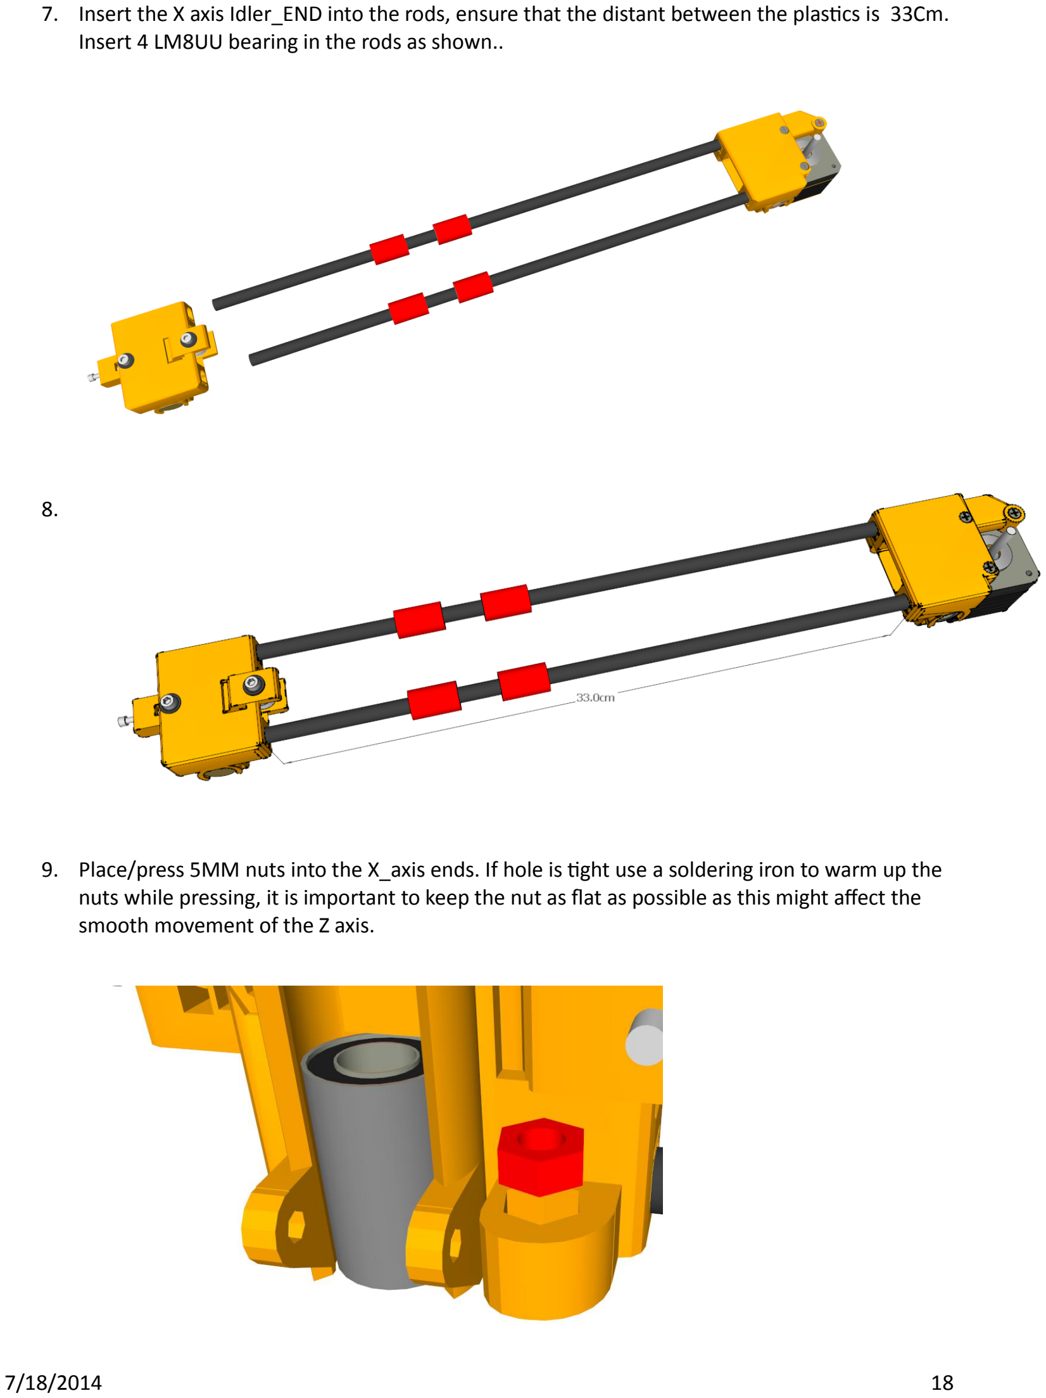
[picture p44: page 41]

7. Insert the X axis Idler_END into the rods, ensure that the distant between the plastics is 33Cm. Insert 4 LM8UU bearing in the rods as shown..

8.

9. Place/press 5MM nuts into the X_axis ends. If hole is tight use a soldering iron to warm up the nuts while pressing, it is important to keep the nut as flat as possible as this might affect the smooth movement of the Z axis.

# THE BUILD… PART 4 (ASSEMBLING THE Z AXIS)

In this part of the build you will put together the Z axis by installing first the two side pipes and then the motors.

1. Insert the Z_Foot_Cap into each of the Z Pipes

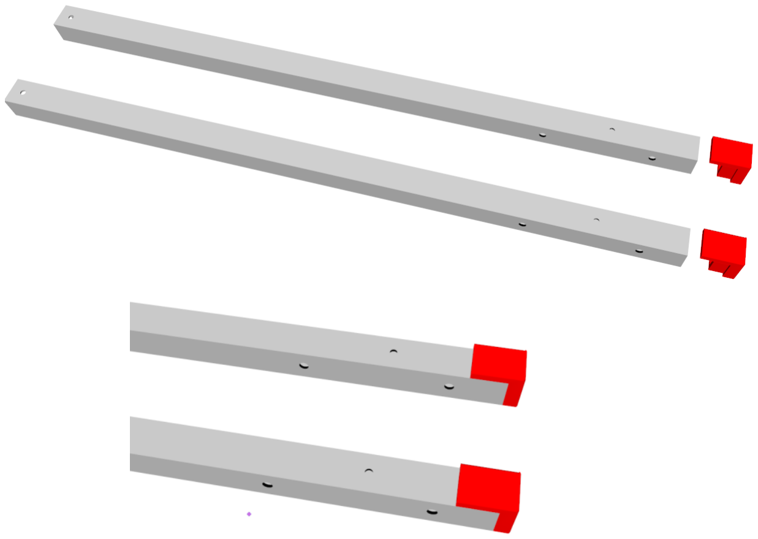
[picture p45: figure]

2. Mount and screw the two side pipes, take note of the hole facing

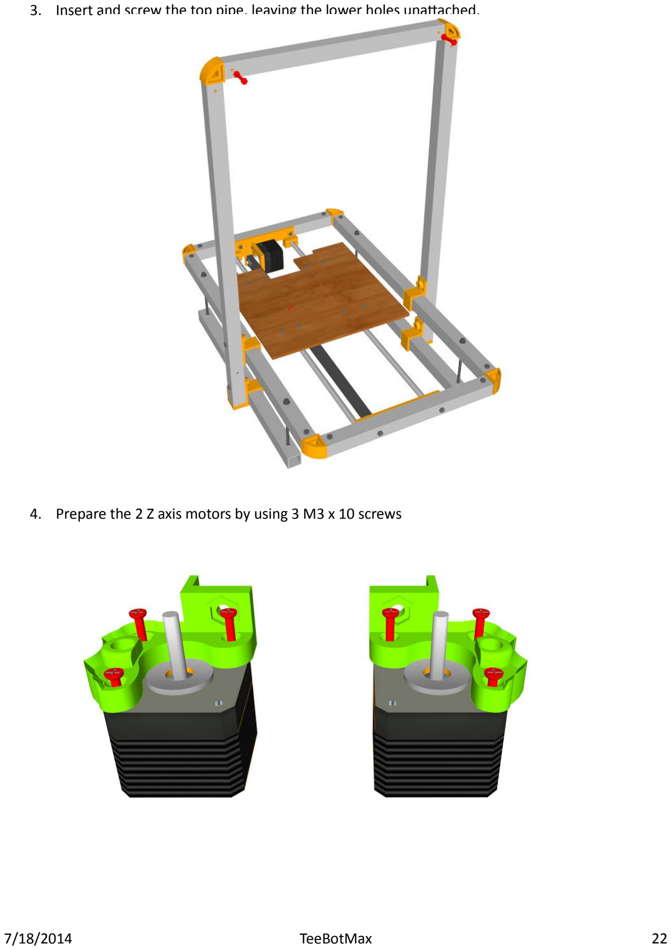
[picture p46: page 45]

3. Insert and screw the top pipe, leaving the lower holes unattached.
4. Prepare the 2 Z axis motors by using 3 M3 x 10 screws

5. Insert the flexible shaft couplers half way and tighten them
6. Install the assembled motors.Not the direction it is facing!!

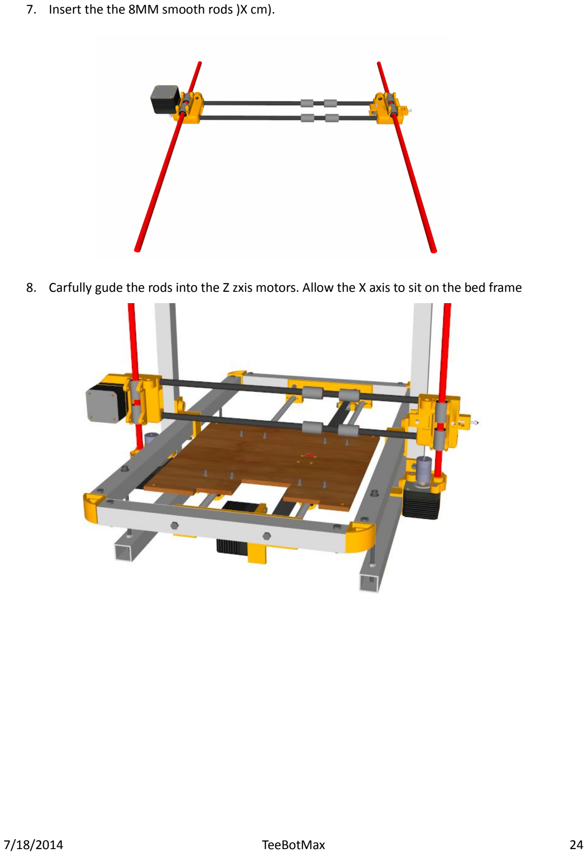
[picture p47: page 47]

7. Insert the the 8MM smooth rods )X cm).
8. Carfully gude the rods into the Z zxis motors. Allow the X axis to sit on the bed frame

9. Tread in the 5MM threaded rod on eacn axis and lock it in place using the grub screw on the coupler.

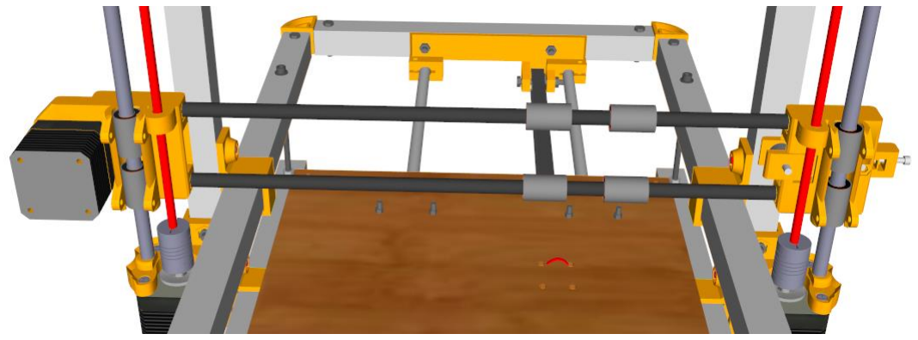
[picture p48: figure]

10. Place the Z_Rod_Holders on each side and lock in place using the 5MM x 6cm screew.

Congrats if you made it this far !!

# THE BUILD PART 5 (EXTRUDER CARRIAGE & BELT)

1. Place the X_Carriage over the 4 pcs of bearing and tie in-place using zip ties

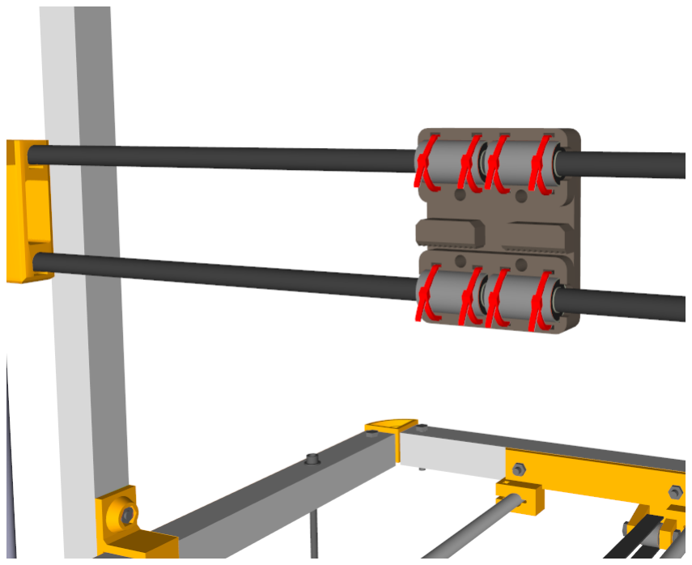
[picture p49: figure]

2. Insert the X axis pulley and lock it in place after centralizing it through the belt passage way.

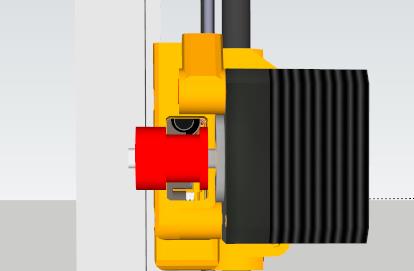
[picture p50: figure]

3. Pass the belt through both X ends and as tight as you can, then tension the belt using the 4MM screw on the belt tensioner

4. Assemble the Extruder sit and fan as shown below.

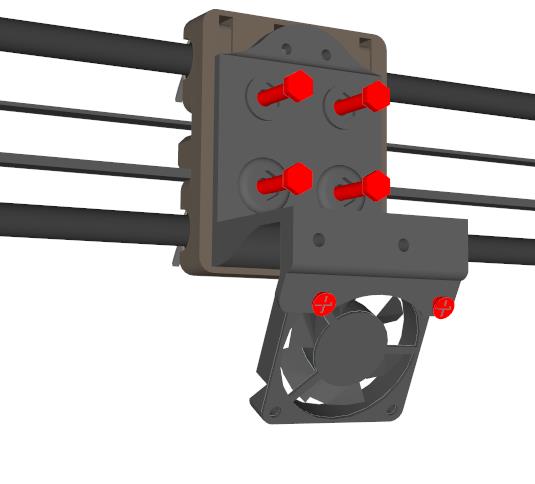
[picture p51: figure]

5. If you are using the Teestruder direc drive extruder with j type hot end, assemble the extruder using the guide here reprap wiki TeeStruder (http://reprap.org/wiki/TeeStruder).

6. Mount the assembled extruder on then extruder sit.

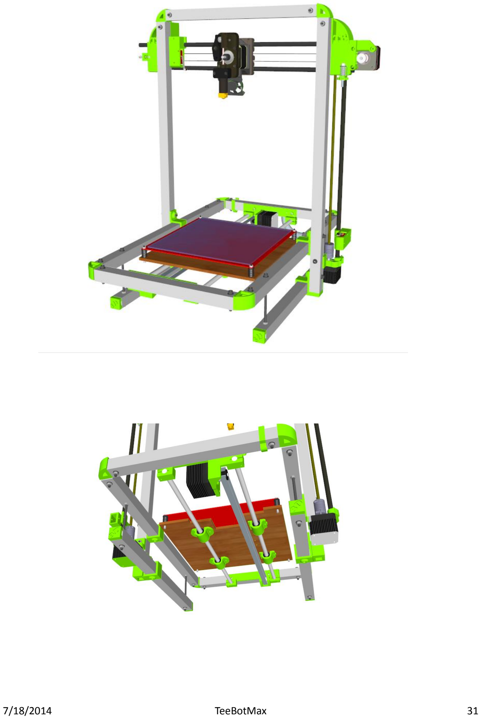
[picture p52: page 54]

# THE BUILD PART 6 (ELECTRONICS & LIMIT SWITCH)

How you wire/connect the electronics of the printed heavily depends on the type of control board you use.

Here is a schema overview for the most common board, RAMPS1.4

LIMIT SWITCH

### 1. X Axis

The X axis Limit switch can be hanged as shown below. I have seen a lot of variation of how this is done the most important thing is to ensure that the X carriage hits the switch.

### 2. Z axis & Smart Z Level

The Z axis limit switch works together with the Smart Z level to allow for easy Z level adjustment. Assemble the Smart level kit as shown. Adjusting the print height (Z axis home) is just a matter of twisting the knob!!. The smart Z level can be glued to the X axis motor end.

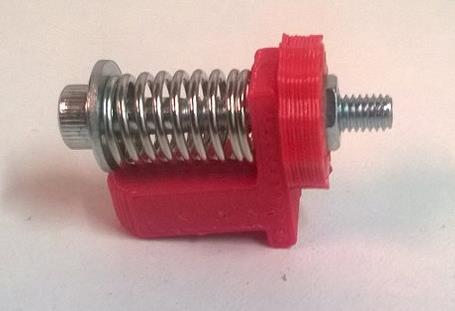
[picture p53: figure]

### 3. Y Axis

Mounting the Y axis limit switch can be done in two ways. You and mount the switch directly on the frame pipe using a zip tie as seen below

If you do not like the cable/ limit switch to be seen you can improvise by mounting the switch under the heat bed on the 8mm smooth rod as seen below using a zip tie to hold the plastic and switch in place tight..

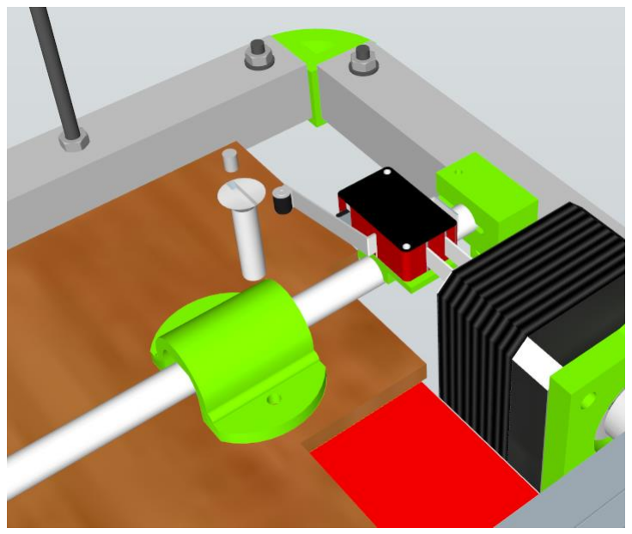
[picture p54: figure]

The firmware: this is the peace of code in the control board that interprets movements and instruction. If you are new to 3D printing I advise you use Sprinter (https://github.com/kliment/Sprinter) and later move to use Erik Zalm marlin, (https://github.com/ErikZalm/Marlin) which basically sprinter on steroids.

The weblog contains a link to where you can download Marlin which is already configured for TeeBotMax.

The kit supply should already have been flashed with the correct marlin firmware.

I separated the board from the printer using 37 pin Dsub connector, this allows for easy packing of the 3D printer, also you can use the same electronics board for more than one 3D printer.

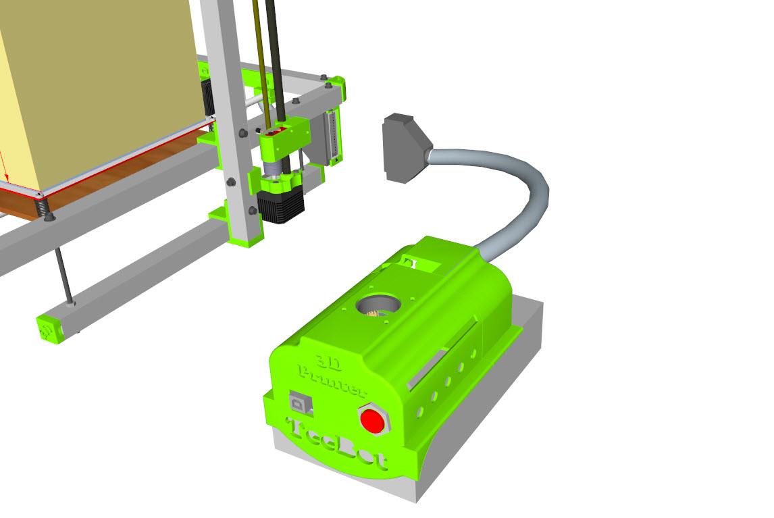
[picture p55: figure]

I hope this guide helps or inspire you in building or assembling your own 3D printer!! If you do please send me a photo of your build.

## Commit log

2014-07-25 Uploaded STL and build manual
    Uploaded STL files and build manual
    [Bearing_Holder.stl, Bed_Knobs.stl, Belt_Bearing_Holder.stl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]
2014-08-06 Updated part list
    Added heat bed plate, clips & bolts.
2014-08-14 Fix broken lines
    Fix broken lines
    [X_Ends_R.stl]
2014-08-25 Update to documentation
    Added new fasteners section, added more detail to the heat bed
    platform.
2014-09-20 Fixed holes
    Missing holes in the Z_rod holder is added, 2 part Ramps casing added,
    extruder extension added.
    [Extruder Extension.stl, Ramps_casing.stl, Z_Rod_Holder_L.stl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]
2014-10-15 Fixed all files for holes.
    [Bearing_Holder.stl, Bed_Knobs.stl, Belt_Bearing_Holder.stl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]
2014-11-10 Added firmware Marlin and limit switch illustration
    Update Firmware and limit switch illustration, adding photos on how to
    mount the switches, added information on the smart Z level kit. Extruder
    mount 2 for longer motors.
    [Smart_Zlevel.stl, X_Extruder_Mount_2.stl]
2016-11-30 Added Teestruder for the TeeBotMax V2
    Added Teestruder for the TeeBotMax V2
    [Extruder_E3d_Lite.stl, SPOOL_FEEDER.stl]
